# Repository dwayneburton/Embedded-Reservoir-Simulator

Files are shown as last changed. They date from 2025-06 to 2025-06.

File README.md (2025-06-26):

# Embedded Reservoir Simulator
STM32 embedded system project developed in C for the NUCLEO-F401RE microcontroller using STM32CubeIDE. The system simulates a dynamic water reservoir by integrating a servo motor, DC pump motor, ultrasonic distance sensor, RPM sensor, and 7-segment display, all wired on a breadboard. Real-time system data such as water level and motor speed is transmitted via UART and monitored using PuTTY. A corresponding schematic and PCB layout were designed to support hardware integration and future PCB fabrication. 

Reservoir_System
Reservoir_Output
Plant_PCB_Layout
Plant_Schematic
Reservoir_3D-Visual_Top
Reservoir_3D-Visual_Bottom

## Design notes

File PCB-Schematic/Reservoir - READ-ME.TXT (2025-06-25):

LABCENTER PROTEUS TOOL INFORMATION FILE
=======================================

In case of difficulty, please e-mail support@labcenter.co.uk

Tool set up for Proteus layout 'Reservoir.pdsprj'.
CADCAM generated at 2:26:22 PM on November 30, 2024.

File List
---------
Top Copper              : Reservoir - Copper (Top).GBR
Bottom Copper           : Reservoir - Copper (Bottom).GBR
Top Silk Screen         : Reservoir - Silk Screen (Top).GBR
Bottom Silk Screen      : Reservoir - Silk Screen (Bottom).GBR
Top Solder Resist       : Reservoir - Solder Resist (Top).GBR
Bottom Solder Resist    : Reservoir - Solder Resist (Bottom).GBR
Top SMT Paste           : Reservoir - SMT Paste (Top).GBR
Bottom SMT Paste        : Reservoir - SMT Paste (Bottom).GBR
Mechanical 1            : Reservoir - Mechanical.GBR
Top Assembly            : Reservoir - Assembly (Top).GBR
Bottom Assembly         : Reservoir - Assembly (Bottom).GBR
Drill, Plated, 1-16     : Reservoir - Drill Top-Bottom Plated.GBR
Netlist                 : Reservoir - Netlist.IPC

Photoplotter Setup
------------------
Format: X2, ASCII, 4.3, metric, absolute, eob=*, LZO
Bounds: -35mm -32mm 35mm 30mm
Notes:  D=Diameter, S=Side, W=Width, H=Height, C=Chamfer, I=Index

D10	CIRCLE  D=0.381mm                                                         DRAW  Conductor
D11	CIRCLE  D=0.305mm                                                         DRAW  Conductor
D12	CIRCLE  D=0.203mm                                                         DRAW  Conductor
D13	CIRCLE  D=0.152mm                                                         DRAW  Conductor
D14	CIRCLE  D=1.016mm                                                         FLASH ViaPad
D15	CIRCLE  D=0.508mm                                                         FLASH ViaPad
D16	SQUARE  S=1.27mm                                                          FLASH ComponentPad
D17	CIRCLE  D=1.524mm                                                         FLASH ComponentPad
D18	SQUARE  S=2.032mm                                                         FLASH ComponentPad
D19	CIRCLE  D=2.032mm                                                         FLASH ComponentPad
D70	RECT    W=1.27mm              H=3.048mm                                   FLASH SMDPad,CuDef
D71	RECT    W=0.635mm             H=2.032mm                                   FLASH SMDPad,CuDef
D20	RECT    W=2.032mm             H=0.635mm                                   FLASH SMDPad,CuDef
D21	SQUARE  S=0.61mm                                                          FLASH SMDPad,CuDef
D22	CIRCLE  D=0.203mm                                                         DRAW  Profile
D23	RECT    W=0.61mm              H=0.559mm                                   FLASH SMDPad,CuDef
D24	RECT    W=0.559mm             H=0.61mm                                    FLASH SMDPad,CuDef
D25	CIRCLE  D=0.203mm                                                         DRAW  Material
D26	CIRCLE  D=1.27mm                                                          FLASH Material
D27	CIRCLE  D=0.813mm                                                         FLASH Material
D28	PPAD    W=1.524mm             H=1.524mm             I=0                   FLASH Material
D29	CIRCLE  D=1.778mm                                                         FLASH Material
D72	PPAD    W=2.286mm             H=2.286mm             I=1                   FLASH Material
D73	CIRCLE  D=2.286mm                                                         FLASH Material
D30	PPAD    W=2.286mm             H=2.286mm             I=2                   FLASH Material
D31	PPAD    W=1.524mm             H=3.302mm             I=3                   FLASH Material
D32	PPAD    W=0.889mm             H=2.286mm             I=4                   FLASH Material
D33	PPAD    W=2.286mm             H=0.889mm             I=5                   FLASH Material
D34	PPAD    W=0.61mm              H=0.61mm              I=6                   FLASH Material
D35	PPAD    W=0.889mm             H=2.286mm             I=7                   FLASH Material
D36	PPAD    W=0.61mm              H=0.559mm             I=8                   FLASH Material
D37	PPAD    W=0.61mm              H=0.61mm              I=9                   FLASH Material
D38	PPAD    W=0.559mm             H=0.61mm              I=10                  FLASH Material
D39	RECT    W=1.27mm              H=3.048mm                                   FLASH Material
D40	RECT    W=0.635mm             H=2.032mm                                   FLASH Material
D41	RECT    W=2.032mm             H=0.635mm                                   FLASH Material
D42	SQUARE  S=0.61mm                                                          FLASH Material
D43	RECT    W=0.61mm              H=0.559mm                                   FLASH Material
D44	RECT    W=0.559mm             H=0.61mm                                    FLASH Material
D45	CIRCLE  D=0.203mm                                                         DRAW  Slot
D46	CIRCLE  D=0.813mm                                                         DRAW  Material
D47	CIRCLE  D=0.178mm                                                         DRAW  Material
D48	CIRCLE  D=0.33mm                                                          DRAW  Material
D49	CIRCLE  D=0.22mm                                                          DRAW  Material
D50	CIRCLE  D=0.212mm                                                         DRAW  Material
D51	CIRCLE  D=0.051mm                                                         DRAW  Material
D52	CIRCLE  D=1.143mm                                                         DRAW  Material
D53	CIRCLE  D=0.269mm                                                         DRAW  Material
D54	CIRCLE  D=0.572mm                                                         DRAW  Material
D55	CIRCLE  D=0.301mm                                                         DRAW  Material
D56	CIRCLE  D=0.235mm                                                         DRAW  Material
D57	CIRCLE  D=0.05mm                                                          DRAW  Material
D58	CIRCLE  D=0.244mm                                                         DRAW  Material
D59	CIRCLE  D=0.035mm                                                         DRAW  Material
D60	CIRCLE  D=0.085mm                                                         DRAW  Material
D61	CIRCLE  D=0.508mm                                                         DRAW  Material
D62	CIRCLE  D=0.461mm                                                         DRAW  Material
D63	CIRCLE  D=0.473mm                                                         DRAW  Material
D64	CIRCLE  D=0.268mm                                                         DRAW  Material
D65	CIRCLE  D=0.038mm                                                         DRAW  Material
D66	CIRCLE  D=0.381mm                                                         FLASH ViaDrill
D67	CIRCLE  D=0.254mm                                                         FLASH ViaDrill
D68	CIRCLE  D=0.762mm                                                         FLASH ComponentDrill
D69	CIRCLE  D=0.889mm                                                         FLASH ComponentDrill
D74	CIRCLE  D=1.016mm                                                         FLASH ComponentDrill

Layer Stackup
-------------
Top Solder Resist        : 0.01mm     Resist
Top Copper               : 0.035mm    Copper
Core                     : 1.6mm      FR4
Bottom Copper            : 0.035mm    Copper
Bottom Solder Resist     : 0.01mm     Resist

[END OF FILE]

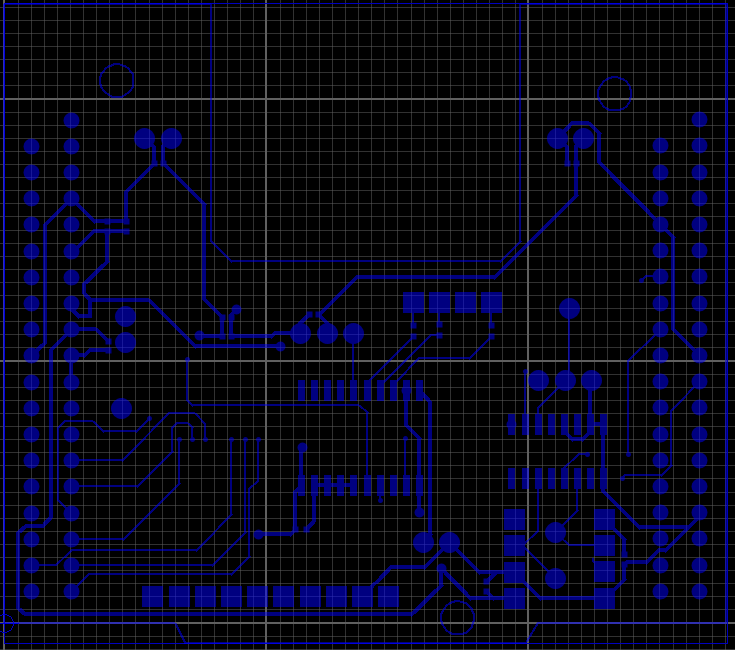
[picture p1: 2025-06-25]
PCB-Schematic/Pictures/Copper (Bottom).PNG

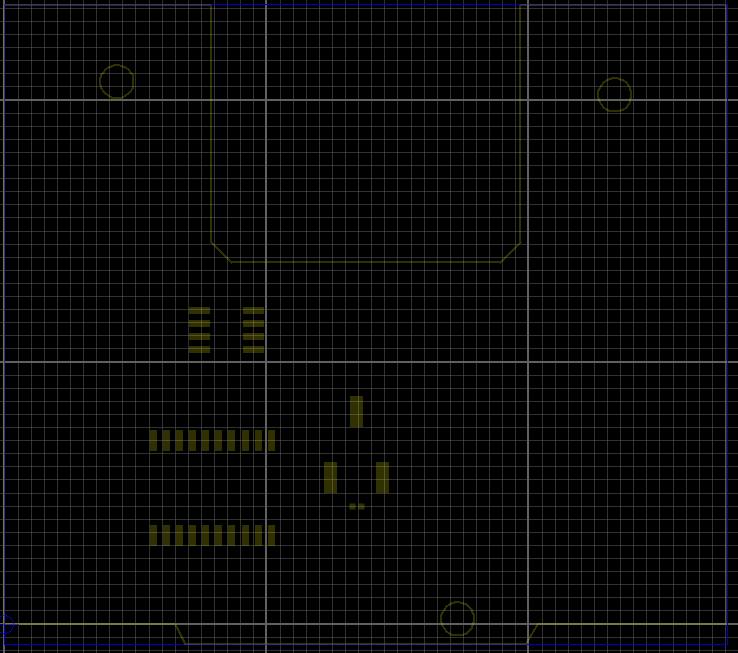
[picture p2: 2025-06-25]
PCB-Schematic/Pictures/SMT Paste (Top).PNG

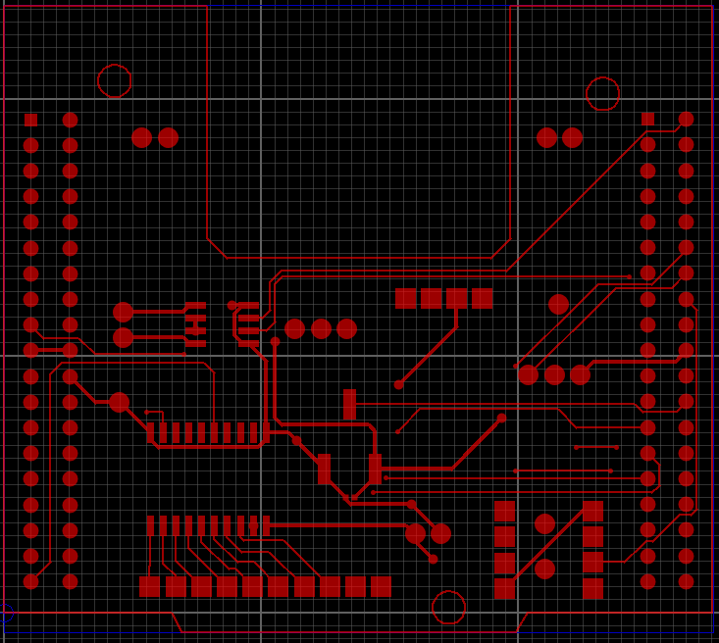
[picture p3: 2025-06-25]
PCB-Schematic/Pictures/Copper (Top).PNG

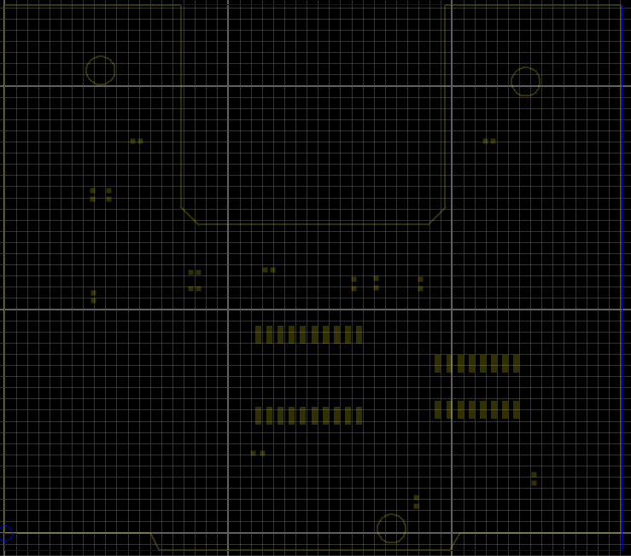
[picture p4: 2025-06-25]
PCB-Schematic/Pictures/SMT Paste (Bottom).PNG

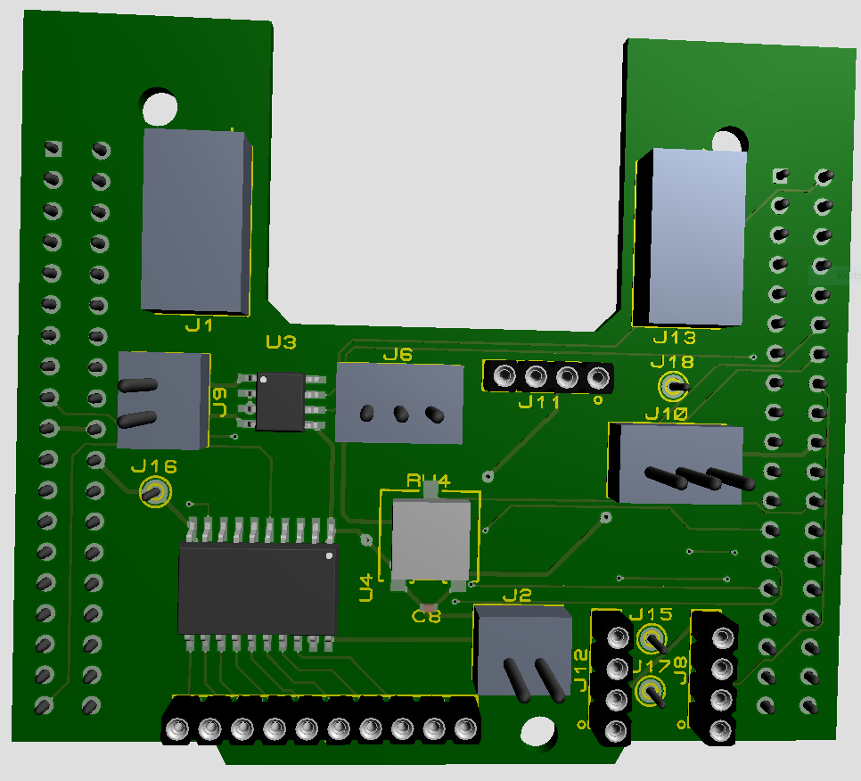
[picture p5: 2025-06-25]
PCB-Schematic/Pictures/3D-Visual (Top).PNG

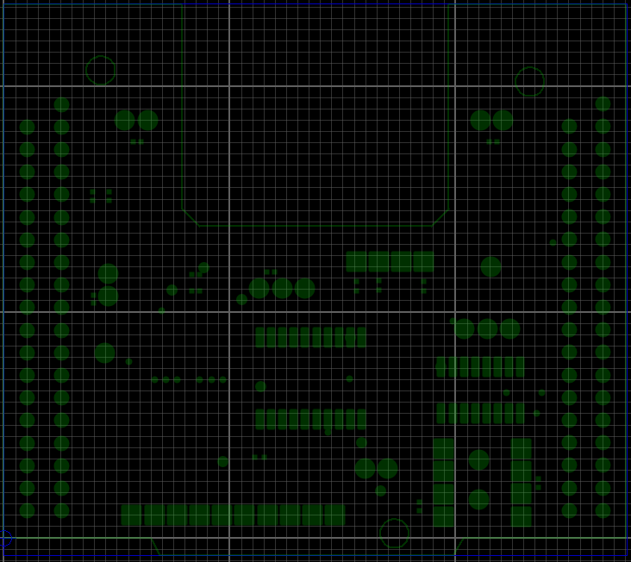
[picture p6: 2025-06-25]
PCB-Schematic/Pictures/Bottom_Resist.PNG

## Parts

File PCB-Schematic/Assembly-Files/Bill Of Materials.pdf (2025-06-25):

## Bill Of Materials for ECE298_RS_ADAPTER

Design Title | ECE298_RS_ADAPTER

### Author Document Number Revision

Design Created | July 7, 2023

### Design Last Modified November 30, 2024 Total Parts In Design 36

11 Capacitors
Quantity | References | Value
2 | C1,C9 | 10000pF
9 | C2-C3,C5-C8,C10-C12 | 100uF
Sub-totals:
4 Resistors
Quantity | References | Value
2 | R1,R3 | 80
1 | R2 | 150
1 | R7 | 1000
Sub-totals:
4 Integrated Circuits
Quantity | References | Value
1 | U2 | ECE298_RS_CMOS4050
1 | U3 | ECE298_RS_L9110
2 | U4-U5 | ECE298_RS_74HCT541
Sub-totals:
17 Miscellaneous
Quantity | References | Value
2 | CN7,CN10 | 1-534236-9
2 | J1,J13 | ECE298_RS_BENCH_POWER
1 | J2 | TIMER BOARD POWER
1 | J6 | MG90S Servo
1 | J8 | HCSR04
1 | J9 | DC MOTOR
1 | J10 | UARTPERIPHERAL
1 | J11 | RGB LED
1 | J12 | RPM SENSOR
1 | J14 | TIMER BOARD
4 | J15-J18 | ECE298_TERMINAL_VIA
1 | RV4 | 10K
Sub-totals:

Totals:

| | November 30, 2024 2:31:16 PM

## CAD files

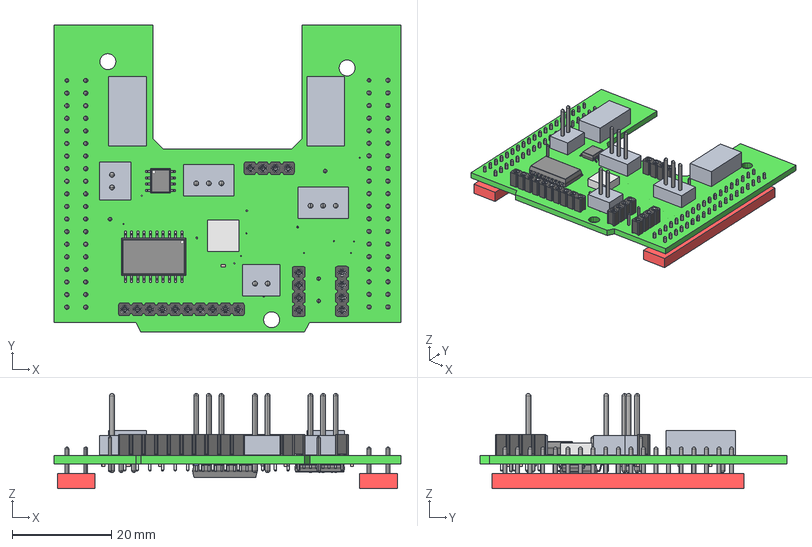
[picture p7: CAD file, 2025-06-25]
PCB-Schematic/Reservoir.STEP
70.0 x 62.0 x 19.2 mm
Layer_1
Pin_1 x 16
Pin_2 x 12
Pin_3 x 4
Pin_4 x 2
Pin_5 x 2
Pin_6 x 2
Pin_7 x 2
Pin_8 x 2
Pin_9 x 2
Pin_10 x 2
Pin_11 x 2
Pin_12 x 2
Pin_13 x 2
Pin_14 x 2
Pin_15 x 2
Pin_16 x 2
Pin_17 x 2
Pin_18 x 2
Pin_19 x 2
Pin_20 x 2
Pin_21 x 2
Pin_22 x 2
Pin_23 x 2
Pin_24 x 2
Pin_25 x 2
Pin_26 x 2
Pin_27 x 2
Pin_28 x 2
Pin_29 x 2
Pin_30 x 2
Pin_31 x 2
Pin_32 x 2
Pin_33 x 2
Pin_34 x 2
Pin_35 x 2
Pin_36 x 2
Pin_37 x 2
Pin_38 x 2

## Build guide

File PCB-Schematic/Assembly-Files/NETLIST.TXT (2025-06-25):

ISIS SCHEMATIC DESCRIPTION FORMAT 8.0
=====================================
Design:   Reservoir
Doc. no.: <NONE>
Revision: <NONE>
Author:   <NONE>
Created:  2023-07-07
Modified: 2024-11-30

*PROPERTIES,0    

*MODELDEFS,0    

*PARTLIST,36   
C1,ECE298_RS_CAP_0U1,10000pF,CODE="Digikey PCC103BQDKR-ND",EID=1E,PACKAGE=CAPC1005X55
C2,ECE298_RS_CAP_0U1,100uF,CODE="Digikey PCC103BQDKR-ND",EID=1F,PACKAGE=CAPC1005X55
C3,ECE298_RS_CAP_0U1,100uF,CODE="Digikey PCC103BQDKR-ND",EID=3,PACKAGE=CAPC1005X55
C5,ECE298_RS_CAP_0U1,100uF,CODE="Digikey PCC103BQDKR-ND",EID=4,PACKAGE=CAPC1005X55
C6,ECE298_RS_CAP_0U1,100uF,CODE="Digikey PCC103BQDKR-ND",EID=5,PACKAGE=CAPC1005X55
C7,ECE298_RS_CAP_0U1,100uF,CODE="Digikey PCC103BQDKR-ND",EID=E,PACKAGE=CAPC1005X55
C8,ECE298_RS_CAP_0U1,100uF,CODE="Digikey PCC103BQDKR-ND",EID=11,PACKAGE=CAPC1005X55
C9,ECE298_RS_CAP_0U1,10000pF,CODE="Digikey PCC103BQDKR-ND",EID=12,PACKAGE=CAPC1005X55
C10,ECE298_RS_CAP_0U1,100uF,CODE="Digikey PCC103BQDKR-ND",EID=13,PACKAGE=CAPC1005X55
C11,ECE298_RS_CAP_0U1,100uF,CODE="Digikey PCC103BQDKR-ND",EID=14,PACKAGE=CAPC1005X55
C12,ECE298_RS_CAP_0U1,100uF,CODE="Digikey PCC103BQDKR-ND",EID=15,PACKAGE=CAPC1005X55
CN7,1-534236-9,1-534236-9,CODE=1-534236-9,EID=25,PACKAGE=ECE298_REVTRANS38DIL-1,SUPPLIER=TE_CONNECTIVITY
CN10,1-534236-9,1-534236-9,CODE=1-534236-9,EID=29,PACKAGE=ECE298_REVTRANS38DIL-1,SUPPLIER=TE_CONNECTIVITY
J1,ECE298_RS_BENCH_POWER,ECE298_RS_BENCH_POWER,EID=1D,PACKAGE=SIL-100-02R
J2,ECE298_RS_2PINHDR,"TIMER BOARD POWER",EID=20,PACKAGE=SIL-100-02
J6,ECE298_RS_3PINHDR,"MG90S Servo",EID=6,PACKAGE=SIL-100-03
J8,ECE298_RS_4PINREC,HCSR04,EID=7,PACKAGE=CONN-SIL4
J9,ECE298_RS_2PINHDR,"DC MOTOR",EID=8,PACKAGE=SIL-100-02
J10,ECE298_RS_3PINHDR,"UART PERIPHERAL",EID=B,PACKAGE=SIL-100-03
J11,ECE298_RS_4PINREC,"RGB LED",EID=C,PACKAGE=CONN-SIL4
J12,ECE298_RS_4PINREC,"RPM SENSOR",EID=D,PACKAGE=CONN-SIL4
J13,ECE298_RS_BENCH_POWER,ECE298_RS_BENCH_POWER,EID=F,PACKAGE=SIL-100-02R
J14,ECE298_RS_10PINREC,"TIMER BOARD",EID=10,PACKAGE=CONN-SIL10
J15,ECE298_TERMINAL_VIA,ECE298_TERMINAL_VIA,EID=17,PACKAGE=PIN
J16,ECE298_TERMINAL_VIA,ECE298_TERMINAL_VIA,EID=18,PACKAGE=PIN
J17,ECE298_TERMINAL_VIA,ECE298_TERMINAL_VIA,EID=19,PACKAGE=PIN
J18,ECE298_TERMINAL_VIA,ECE298_TERMINAL_VIA,EID=1A,PACKAGE=PIN
R1,9C04021A1500JLHF3,80,CODE="Digikey 311-150JDKR-ND",EID=1,PACKAGE=RESC1005X40,PRIMTYPE=RESISTOR
R2,9C04021A1800JLHF3,150,CODE="Digikey 311-180JCT-ND",EID=2,PACKAGE=RESC1005X40,PRIMTYPE=RESISTOR
R3,9C04021A1500JLHF3,80,CODE="Digikey 311-150JDKR-ND",EID=24,PACKAGE=RESC1005X40,PRIMTYPE=RESISTOR
R7,9C04021A1500JLHF3,1000,CODE="Digikey 311-150JDKR-ND",EID=1B,PACKAGE=RESC1005X40,PRIMTYPE=RESISTOR
RV4,ECE298_RS_POT10K,10K,CODE="Digikey 3361P-103GLFDKR-ND",EID=9,PACKAGE=TRIM_3361P,STATE=5
U2,ECE298_RS_CMOS4050,ECE298_RS_CMOS4050,EID_A=21,EID_B=22,EID_C=23,EID_D=26,EID_E=27,EID_F=28,ITFMOD=CMOS,MODFILE=40BUF,PACKAGE=SO16,VDD=+3.3V,VSS=GND
U3,ECE298_RS_L9110,ECE298_RS_L9110,EID=A,ITFMOD=TTL,PACKAGE=SO8
U4,ECE298_RS_74HCT541,ECE298_RS_74HCT541,EID=16,GND=GND,PACKAGE=SO20W,PINSWAP="1,19",VCC=+5.0V
U5,ECE298_RS_74HCT541,ECE298_RS_74HCT541,EID=1C,GND=GND,PACKAGE=SO20W,PINSWAP="1,19",VCC=+5.0V

*NETLIST,47   
GRN,3,CLASS=SIGNAL
GRN,LBL
R1,PS,1
J11,PS,4

GRN_5V,3,CLASS=SIGNAL
GRN_5V,LBL
R1,PS,2
U5,TS,16

RED,3,CLASS=SIGNAL
RED,LBL
R2,PS,1
J11,PS,3

RED_5V,3,CLASS=SIGNAL
RED_5V,LBL
R2,PS,2
U5,TS,17

PWM,3,CLASS=SIGNAL
PWM,LBL
J6,PS,3
U5,TS,15

ECHO,4,CLASS=SIGNAL
ECHO,LBL
J8,PS,3
J15,PS,1
U2,IP,11

OA,3,CLASS=POWER
OA,LBL
J9,PS,1
U3,OP,1

OB,3,CLASS=POWER
OB,LBL
J9,PS,2
U3,OP,4

RXD,4,CLASS=SIGNAL
RXD,LBL
J10,PS,2
U2,IP,3
J18,PS,1

BLU,3,CLASS=SIGNAL
BLU,LBL
J11,PS,1
R3,PS,1

D0,4,CLASS=SIGNAL
D0,LBL
J12,PS,3
J17,PS,1
U2,IP,14

DIGIT_A3,3,CLASS=SIGNAL
DIGIT_A3,LBL
U4,TS,18
J14,PS,3

DIGIT_A2,3,CLASS=SIGNAL
DIGIT_A2,LBL
U4,TS,17
J14,PS,4

DIGIT_A1,3,CLASS=SIGNAL
DIGIT_A1,LBL
U4,TS,16
J14,PS,5

DIGIT_A0,3,CLASS=SIGNAL
DIGIT_A0,LBL
U4,TS,15
J14,PS,6

DIGIT_B3,3,CLASS=SIGNAL
DIGIT_B3,LBL
U4,TS,14
J14,PS,7

DIGIT_B2,3,CLASS=SIGNAL
DIGIT_B2,LBL
U4,TS,13
J14,PS,8

DIGIT_B1,3,CLASS=SIGNAL
DIGIT_B1,LBL
U4,TS,12
J14,PS,9

DIGIT_B0,3,CLASS=SIGNAL
DIGIT_B0,LBL
U4,TS,11
J14,PS,10

DRAIN,6,CLASS=POWER
DRAIN,LBL
R7,PS,1
U5,IP,6
U5,IP,7
U5,IP,8
U5,IP,9

BLU_5V,3,CLASS=SIGNAL
BLU_5V,LBL
U5,TS,18
R3,PS,2

PA0,3,CLASS=SIGNAL
PA0,GT
CN7,PS,28
U4,IP,6

PA1,3,CLASS=SIGNAL
PA1,GT
CN7,PS,30
U4,IP,7

PA4,3,CLASS=SIGNAL
PA4,GT
CN7,PS,32
U4,IP,9

PB0,3,CLASS=SIGNAL
PB0,GT
CN7,PS,34
U4,IP,8

PC2,3,CLASS=SIGNAL
PC2,GT
CN7,PS,35
U4,IP,4

PC1,3,CLASS=SIGNAL
PC1,GT
CN7,PS,36
U4,IP,3

PC3,3,CLASS=SIGNAL
PC3,GT
CN7,PS,37
U4,IP,5

PC0,3,CLASS=SIGNAL
PC0,GT
CN7,PS,38
U4,IP,2

PA12,3,CLASS=SIGNAL
PA12,GT
CN10,PS,12
U2,OP,2

PA6,4,CLASS=SIGNAL
PA6,GT
PWM CH1,LBL
CN10,PS,13
U3,IP,6

PA11,4,CLASS=SIGNAL
PA11,GT
TXD,LBL
CN10,PS,14
J10,PS,1

PB12,4,CLASS=SIGNAL
PB12,GT
TRIG,LBL
CN10,PS,16
J8,PS,2

PC8,4,CLASS=SIGNAL
PC8,GT
PWM CH2,LBL
CN10,PS,2
U3,IP,7

PB1,3,CLASS=SIGNAL
PB1,GT
CN10,PS,24
RV4,PS,3

PB10,3,CLASS=SIGNAL
PB10,GT
CN10,PS,25
U5,IP,2

PB4,3,CLASS=SIGNAL
PB4,GT
CN10,PS,27
U5,IP,4

PB5,3,CLASS=SIGNAL
PB5,GT
CN10,PS,29
U5,IP,3

PA15,3,CLASS=SIGNAL
PA15,GT
CN7,PS,17
U5,IP,5

PB2,3,CLASS=SIGNAL
PB2,GT
U2,OP,15
CN10,PS,22

PB6,3,CLASS=SIGNAL
PB6,GT
U2,OP,12
CN10,PS,17

{NC},58
A0,LBL
J14,PS,1
U2,PS,13
U2,PS,16
U2,OP,6
U2,OP,4
CN10,PS,31
U2,OP,10
CN10,PS,15
CN10,PS,37
CN10,PS,35
CN10,PS,34
CN10,PS,30
CN10,PS,28
CN10,PS,33
CN10,PS,26
CN10,PS,23
CN10,PS,21
CN10,PS,19
CN10,PS,18
CN10,PS,11
CN10,PS,6
CN10,PS,5
CN10,PS,4
CN10,PS,3
CN10,PS,1
CN7,PS,1
CN7,PS,2
CN7,PS,3
CN7,PS,13
CN7,PS,15
CN7,PS,21
CN7,PS,23
CN7,PS,14
CN10,PS,8
CN10,PS,7
CN10,PS,38
CN10,PS,36
CN10,PS,10
CN7,PS,9
CN7,PS,7
CN7,PS,6
CN7,PS,5
CN7,PS,4
CN7,PS,33
CN7,PS,31
CN7,PS,29
CN7,PS,27
CN7,PS,26
CN7,PS,25
CN7,PS,24
CN7,PS,11
CN7,PS,10
U5,TS,14
U5,TS,13
U5,TS,12
U5,TS,11
J12,PS,4

+3.3V,8,CLASS=POWER
+3.3V,PR
U2,PP,1
CN7,PS,16
CN7,PS,12
C8,PS,1
RV4,PS,2
C5,PS,1
C2,PS,1

+5.0V,11,CLASS=POWER
+5.0V,PR
VCC,LBL
CN7,PS,18
J2,PS,1
U5,PP,20
U4,PP,20
J12,PS,1
C11,PS,1
J8,PS,4
C10,PS,1
C6,PS,1

+5V_EXT,5,CLASS=POWER
+5V_EXT,PR
J13,PS,1
C7,PS,1
J6,PS,2
C12,PS,1

+6V_EXT,7,CLASS=POWER
+6V_EXT,PR
U3,PP,2
U3,PP,3
C9,PS,1
C1,PS,1
J1,PS,1
C3,PS,1

GND,43,CLASS=POWER
GND,PR
J14,PS,2
U2,PP,8
U2,IP,7
U2,IP,5
U2,IP,9
CN10,PS,9
CN10,PS,32
CN10,PS,20
CN7,PS,8
CN7,PS,22
CN7,PS,20
CN7,PS,19
J2,PS,2
U5,PP,10
J16,PS,1
U4,PP,10
C12,PS,2
U5,IP,19
U5,IP,1
R7,PS,2
C11,PS,2
C10,PS,2
C9,PS,2
C1,PS,2
U4,IP,1
U4,IP,19
J13,PS,2
C7,PS,2
J12,PS,2
J11,PS,2
J10,PS,3
J8,PS,1
U3,PP,5
U3,PP,8
C8,PS,2
RV4,PS,1
J6,PS,1
C6,PS,2
C5,PS,2
C2,PS,2
C3,PS,2
J1,PS,2

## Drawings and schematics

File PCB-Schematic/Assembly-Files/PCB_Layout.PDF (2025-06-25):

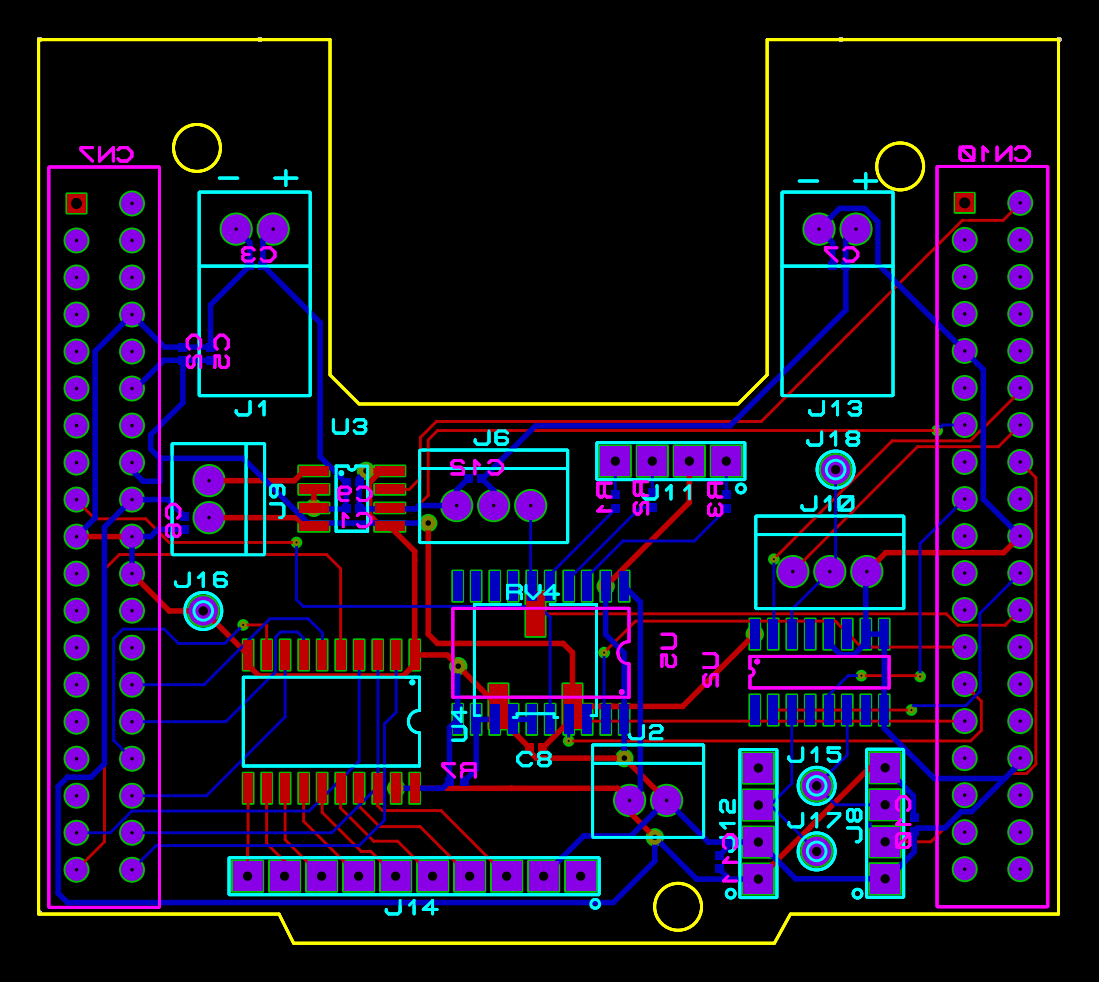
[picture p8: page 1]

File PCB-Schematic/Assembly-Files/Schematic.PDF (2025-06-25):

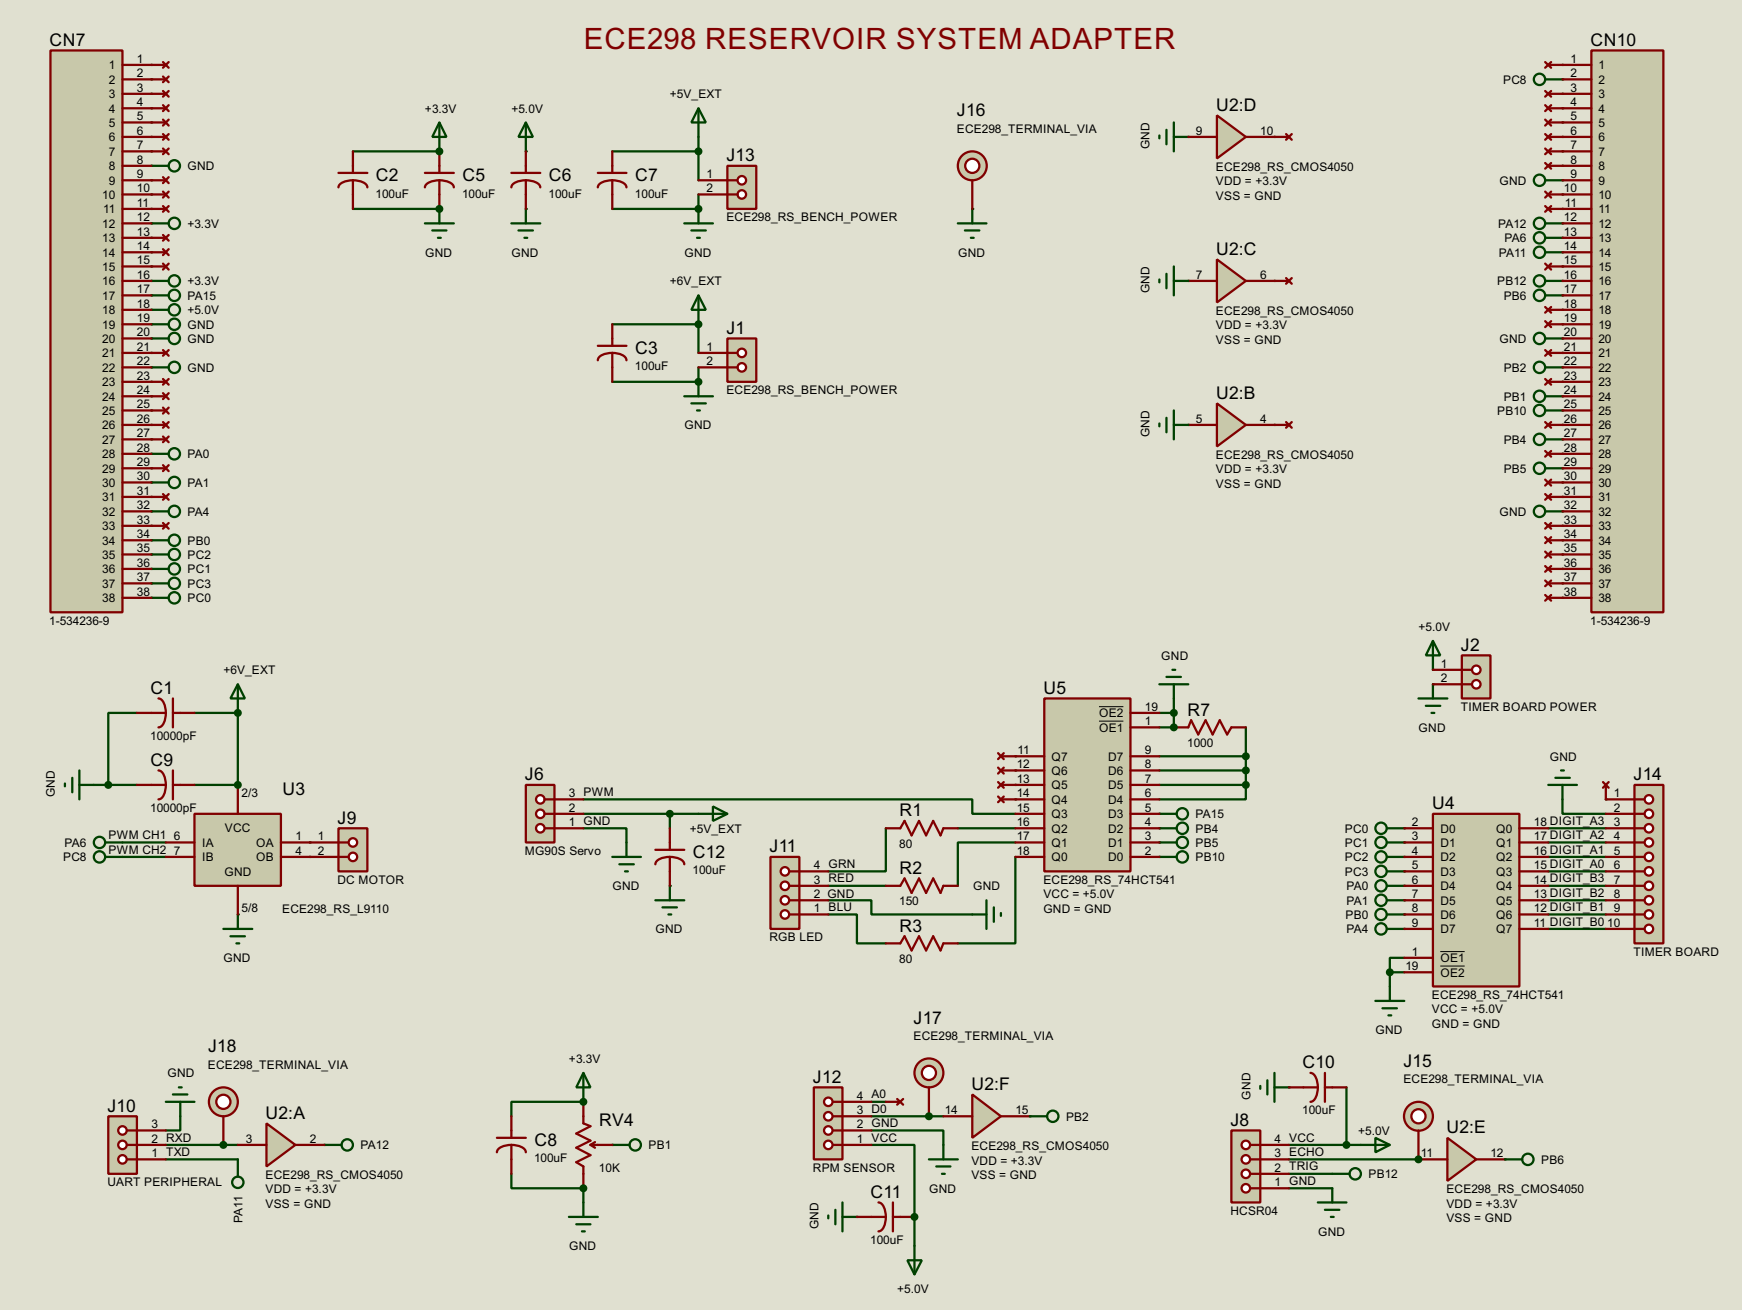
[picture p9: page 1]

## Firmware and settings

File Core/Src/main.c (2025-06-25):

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
/* Includes ------------------------------------------------------------------*/
#include "main.h"

/* USER CODE BEGIN Includes */
#include <string.h>
#include <stdio.h>
#include <time.h>
#include <stdlib.h>
/* USER CODE END Includes */

ADC_HandleTypeDef hadc1;

TIM_HandleTypeDef htim2;
TIM_HandleTypeDef htim3;
TIM_HandleTypeDef htim4;
TIM_HandleTypeDef htim5;

UART_HandleTypeDef huart2;
UART_HandleTypeDef huart6;

/* USER CODE BEGIN PV */
volatile uint8_t clock_hours = 0;
volatile uint8_t clock_mins = 0;
volatile uint8_t clock_secs = 0;
volatile uint8_t wall_clock_hr_update_flag = 0;

volatile uint8_t hcsr04_Rx_flag = 0; // Reset the interrupt flag for the HCSR04
volatile uint8_t first_edge = 0; // Set it back to false
volatile uint16_t time_edge1 = 0;
volatile uint16_t time_edge2 = 0;

volatile uint16_t rpm_tick_count = 0;

uint8_t empty = 0;
uint8_t byte[2];
uint8_t rcv_intpt_flag = 0;
uint8_t txd_msg_buffer[64] = {0};

uint16_t time_diff = 0;
int filled = 0;
int distance = 0;

uint8_t counter_tens = 0;
uint8_t counter_ones = 0;
uint8_t bottom_distance = 65; //distance to bottom in cm
uint8_t top_distance = 10; //distance to top in cm
uint8_t rpm = 0;

int TIM2_CH1_DCVAL = 500;

/* USER CODE END PV */

void SystemClock_Config(void);
static void MX_GPIO_Init(void);
static void MX_USART2_UART_Init(void);
static void MX_USART6_UART_Init(void);
static void MX_ADC1_Init(void);
static void MX_TIM3_Init(void);
static void MX_TIM2_Init(void);
static void MX_TIM4_Init(void);
static void MX_TIM5_Init(void);
/* USER CODE BEGIN PFP */
static void ADC_Select_CH(int CH);
/* USER CODE END PFP */

/* USER CODE BEGIN 0 */


void ADC_Select_CH(int CH)
{
    ADC_ChannelConfTypeDef sConfig = {0};
    switch(CH)
    {
        case 0:
            sConfig.Channel = ADC_CHANNEL_0;
            sConfig.Rank = 1;
            if (HAL_ADC_ConfigChannel(&hadc1, &sConfig) != HAL_OK)
            {
                Error_Handler();
            }
            break;
        case 1:
            sConfig.Channel = ADC_CHANNEL_1;
            sConfig.Rank = 1;
            if (HAL_ADC_ConfigChannel(&hadc1, &sConfig) != HAL_OK)
            {
                Error_Handler();
            }
            break;
        case 2:
            sConfig.Channel = ADC_CHANNEL_2;
            sConfig.Rank = 1;
            if (HAL_ADC_ConfigChannel(&hadc1, &sConfig) != HAL_OK)
            {
                Error_Handler();
            }
            break;
        case 3:
            sConfig.Channel = ADC_CHANNEL_3;
            sConfig.Rank = 1;
            if (HAL_ADC_ConfigChannel(&hadc1, &sConfig) != HAL_OK)
            {
                Error_Handler();
            }
            break;
        case 4:
            sConfig.Channel = ADC_CHANNEL_4;
            sConfig.Rank = 1;
            if (HAL_ADC_ConfigChannel(&hadc1, &sConfig) != HAL_OK)
            {
                Error_Handler();
            }
            break;
        case 5:
            sConfig.Channel = ADC_CHANNEL_5;
            sConfig.Rank = 1;
            if (HAL_ADC_ConfigChannel(&hadc1, &sConfig) != HAL_OK)
            {
                Error_Handler();
            }
            break;
        case 6:
            sConfig.Channel = ADC_CHANNEL_6;
            sConfig.Rank = 1;
            if (HAL_ADC_ConfigChannel(&hadc1, &sConfig) != HAL_OK)
            {
                Error_Handler();
            }
            break;
        case 7:
            sConfig.Channel = ADC_CHANNEL_7;
            sConfig.Rank = 1;
            if (HAL_ADC_ConfigChannel(&hadc1, &sConfig) != HAL_OK)
            {
                Error_Handler();
            }
            break;
        case 8:
            sConfig.Channel = ADC_CHANNEL_8;
            sConfig.Rank = 1;
            if (HAL_ADC_ConfigChannel(&hadc1, &sConfig) != HAL_OK)
            {
                Error_Handler();
            }
            break;
        case 9:
            sConfig.Channel = ADC_CHANNEL_9;
            sConfig.Rank = 1;
            if (HAL_ADC_ConfigChannel(&hadc1, &sConfig) != HAL_OK)
            {
                Error_Handler();
            }
            break;
        case 10:
            sConfig.Channel = ADC_CHANNEL_10;
            sConfig.Rank = 1;
            if (HAL_ADC_ConfigChannel(&hadc1, &sConfig) != HAL_OK)
            {
                Error_Handler();
            }
            break;
        case 11:
            sConfig.Channel = ADC_CHANNEL_11;
            sConfig.Rank = 1;
            if (HAL_ADC_ConfigChannel(&hadc1, &sConfig) != HAL_OK)
            {
                Error_Handler();
            }
            break;
        case 12:
            sConfig.Channel = ADC_CHANNEL_12;
            sConfig.Rank = 1;
            if (HAL_ADC_ConfigChannel(&hadc1, &sConfig) != HAL_OK)
            {
                Error_Handler();
            }
            break;
        case 13:
            sConfig.Channel = ADC_CHANNEL_13;
            sConfig.Rank = 1;
            if (HAL_ADC_ConfigChannel(&hadc1, &sConfig) != HAL_OK)
            {
                Error_Handler();
            }
            break;
        case 14:
            sConfig.Channel = ADC_CHANNEL_14;
            sConfig.Rank = 1;
            if (HAL_ADC_ConfigChannel(&hadc1, &sConfig) != HAL_OK)
            {
                Error_Handler();
            }
            break;
        case 15:
            sConfig.Channel = ADC_CHANNEL_15;
            sConfig.Rank = 1;
            if (HAL_ADC_ConfigChannel(&hadc1, &sConfig) != HAL_OK)
            {
                Error_Handler();
            }
            break;
    }
}


void DIGITS_Display(uint8_t DIGIT)
{
	uint8_t DIGIT_B = DIGIT % 10;
	uint8_t DIGIT_A = (DIGIT - DIGIT_B) / 10;

	uint8_t DIGITA_VAL = 0x0F & DIGIT_A; //mask off higher4 bits
	 int Abit0 = (DIGITA_VAL ) & 1;  	// extract Abit0 of the 4-bit value
	 int Abit1 = (DIGITA_VAL >> 1) & 1;  // extract Abit1 of the 4-bit value
	 int Abit2 = (DIGITA_VAL >> 2) & 1;  // extract Abit2 of the 4-bit value
	 int Abit3 = (DIGITA_VAL >> 3) & 1;  // extract Abit3 of the 4-bit value

	 uint8_t DIGITB_VAL = 0x0F & DIGIT_B; //mask off higher4 bits
	 int Bbit0 = (DIGITB_VAL ) & 1;  	// extract Bbit0 of the 4-bit value
	 int Bbit1 = (DIGITB_VAL >> 1) & 1;  // extract Bbit1 of the 4-bit value
	 int Bbit2 = (DIGITB_VAL >> 2) & 1;  // extract Bbit2 of the 4-bit value
	 int Bbit3 = (DIGITB_VAL >> 3) & 1;  // extract Bbit3 of the 4-bit value

	 if (Abit0 == (0))
	 {
		 HAL_GPIO_WritePin(GPIOC, DIGIT_A0_Pin, GPIO_PIN_RESET);
	 }
	 else
	 {
		 HAL_GPIO_WritePin(GPIOC, DIGIT_A0_Pin, GPIO_PIN_SET);

	 }
	 if (Abit1 == (0))
	 {
		 HAL_GPIO_WritePin(GPIOC, DIGIT_A1_Pin, GPIO_PIN_RESET);
	 }
	 else
	 {
		 HAL_GPIO_WritePin(GPIOC, DIGIT_A1_Pin, GPIO_PIN_SET);

	 }
	 if (Abit2 == (0))
	 {
		 HAL_GPIO_WritePin(GPIOC, DIGIT_A2_Pin, GPIO_PIN_RESET);
	 }
	 else
	 {
		 HAL_GPIO_WritePin(GPIOC, DIGIT_A2_Pin, GPIO_PIN_SET);

	 }
	 if (Abit3 == (0))
	 {
		 HAL_GPIO_WritePin(GPIOC, DIGIT_A3_Pin, GPIO_PIN_RESET);
	 }
	 else
	 {
		 HAL_GPIO_WritePin(GPIOC, DIGIT_A3_Pin, GPIO_PIN_SET);

	 }


	 if (Bbit0 == (0))
	 {
		 HAL_GPIO_WritePin(GPIOA, DIGIT_B0_Pin, GPIO_PIN_RESET);
	 }
	 else
	 {
		 HAL_GPIO_WritePin(GPIOA, DIGIT_B0_Pin, GPIO_PIN_SET);

	 }
	 if (Bbit1 == (0))
	 {
		 HAL_GPIO_WritePin(GPIOB, DIGIT_B1_Pin, GPIO_PIN_RESET);
	 }
	 else
	 {
		 HAL_GPIO_WritePin(GPIOB, DIGIT_B1_Pin, GPIO_PIN_SET);

	 }
	 if (Bbit2 == (0))
	 {
		 HAL_GPIO_WritePin(GPIOA, DIGIT_B2_Pin, GPIO_PIN_RESET);
	 }
	 else
	 {
		 HAL_GPIO_WritePin(GPIOA, DIGIT_B2_Pin, GPIO_PIN_SET);

	 }
	 if (Bbit3 == (0))
	 {
		 HAL_GPIO_WritePin(GPIOA, DIGIT_B3_Pin, GPIO_PIN_RESET);
	 }
	 else
	 {
		 HAL_GPIO_WritePin(GPIOA, DIGIT_B3_Pin, GPIO_PIN_SET);

	 }
}

void HCSR04_TRIG_PULSE(void)
{
	HAL_GPIO_WritePin(HCSR04_TRIG_GPIO_Port, HCSR04_TRIG_Pin, GPIO_PIN_SET);
	for (int j = 0; j != 48; j = j + 1) {}
	HAL_GPIO_WritePin(HCSR04_TRIG_GPIO_Port, HCSR04_TRIG_Pin, GPIO_PIN_RESET);
	HAL_Delay(30);
}

void MOTOR_Run(int speed)
{
	if(speed >= 0) {
		TIM3->CCR3 = ((float)speed/100)*60000;
		TIM3->CCR1 = 0;
	} else {
		TIM3->CCR1 = ((float)speed/-100)*60000;
		TIM3->CCR3 = 0;
	}
}

void SERVO_Run(int position)
{
	int TIM2_CH1_STEP = 20;
	while(TIM2_CH1_DCVAL != position) {
		if(TIM2_CH1_DCVAL < position){
			TIM2_CH1_DCVAL += TIM2_CH1_STEP;
		}else if (TIM2_CH1_DCVAL > position){
			TIM2_CH1_DCVAL -= TIM2_CH1_STEP;
		}
		TIM2->CCR1 = TIM2_CH1_DCVAL;
		HAL_Delay(5);
	}
}

void RGBLED_Run(uint8_t colour)
{
	switch(colour)
	{
	case 0: // purple
		HAL_GPIO_WritePin(GPIOB, BLU_Pin, GPIO_PIN_SET);
		HAL_GPIO_WritePin(GPIOB, GRN_Pin, GPIO_PIN_RESET);
		HAL_GPIO_WritePin(GPIOB, RED_Pin, GPIO_PIN_SET);
		break;
	case 1: // red
		HAL_GPIO_WritePin(GPIOB, BLU_Pin, GPIO_PIN_RESET);
		HAL_GPIO_WritePin(GPIOB, GRN_Pin, GPIO_PIN_RESET);
		HAL_GPIO_WritePin(GPIOB, RED_Pin, GPIO_PIN_SET);
		break;
	case 2: // green
		HAL_GPIO_WritePin(GPIOB, BLU_Pin, GPIO_PIN_RESET);
		HAL_GPIO_WritePin(GPIOB, GRN_Pin, GPIO_PIN_SET);
		HAL_GPIO_WritePin(GPIOB, RED_Pin, GPIO_PIN_RESET);
		break;
	case 3: // blue
		HAL_GPIO_WritePin(GPIOB, BLU_Pin, GPIO_PIN_SET);
		HAL_GPIO_WritePin(GPIOB, GRN_Pin, GPIO_PIN_RESET);
		HAL_GPIO_WritePin(GPIOB, RED_Pin, GPIO_PIN_RESET);
		break;
	case 4: // none
		HAL_GPIO_WritePin(GPIOB, BLU_Pin, GPIO_PIN_RESET);
		HAL_GPIO_WritePin(GPIOB, GRN_Pin, GPIO_PIN_RESET);
		HAL_GPIO_WritePin(GPIOB, RED_Pin, GPIO_PIN_RESET);
		break;
	case 5: // white
		HAL_GPIO_WritePin(GPIOB, BLU_Pin, GPIO_PIN_SET);
		HAL_GPIO_WritePin(GPIOB, GRN_Pin, GPIO_PIN_SET);
		HAL_GPIO_WritePin(GPIOB, RED_Pin, GPIO_PIN_SET);
		break;
	}
}

int generate_random(int min, int max){
	return (rand() % (max-min+1))+ min;
}
/* USER CODE END 0 */

/**
  * @brief  The application entry point.
  * @retval int
  */
int main(void)
{

  /* MCU Configuration--------------------------------------------------------*/

  /* Reset of all peripherals, Initializes the Flash interface and the Systick. */
  HAL_Init();

  /* Configure the system clock */
  SystemClock_Config();

  /* Initialize all configured peripherals */
  MX_GPIO_Init();
  MX_USART2_UART_Init();
  MX_USART6_UART_Init();
  MX_ADC1_Init();
  MX_TIM3_Init();
  MX_TIM2_Init();
  MX_TIM4_Init();
  MX_TIM5_Init();
  /* USER CODE BEGIN 2 */

  HAL_TIM_Base_Start(&htim2);
  HAL_TIM_PWM_Start(&htim2, TIM_CHANNEL_1);
  TIM3->PSC = 16-1;
  TIM3->ARR = 20000-1;
  TIM3->CCR1 = TIM2_CH1_DCVAL;

  //HAL_TIM_Base_Init(&htim3);
  HAL_TIM_PWM_Start(&htim3, TIM_CHANNEL_1);
  HAL_TIM_PWM_Start(&htim3, TIM_CHANNEL_3);
  TIM3->PSC = 0;
  TIM3->ARR = 60000;
  TIM3->CCR1 = 0;
  TIM3->CCR3 = 0;

  HAL_TIM_Base_Init(&htim4);
  HAL_TIM_Base_Start(&htim4);
  HAL_TIM_IC_Start_IT(&htim4, TIM_CHANNEL_1);

  HAL_TIM_Base_Start_IT(&htim5);
  clock_hours = 0;
  clock_mins = 0;
  clock_secs = 0;
  /* USER CODE END 2 */
  /* Infinite loop */
  /* USER CODE BEGIN WHILE */

  uint8_t pipe_connection[4] = {0};
  uint8_t pipe_pwm_mode[4] = {0};
  uint8_t current_time = 0;
  uint8_t start_time[4] = {0};
  uint8_t end_time[4] = {0};

  sprintf((char*)txd_msg_buffer, "\r\n\nSETUP MODE");
  HAL_UART_Transmit(&huart6, txd_msg_buffer, strlen((char*)txd_msg_buffer), 1000);
  HAL_Delay(500);

  sprintf((char*)txd_msg_buffer,"\r\n\nFIRST PIPELINE CHOICE FOR CONNECTION: ");
  HAL_UART_Transmit(&huart6, txd_msg_buffer, strlen((char*)txd_msg_buffer),1000);
  rcv_intpt_flag = 00;
  HAL_UART_Receive_IT(&huart6, &byte, 1);
  while(rcv_intpt_flag == (00)) {}
  pipe_connection[0] = (byte[0]-'0');
  sprintf((char*)txd_msg_buffer,"\r\nFIRST PIPELINE CHOICE FOR MOTOR PWM: ");
  HAL_UART_Transmit(&huart6, txd_msg_buffer, strlen((char*)txd_msg_buffer),1000);
  rcv_intpt_flag = 00;
  HAL_UART_Receive_IT(&huart6, &byte, 2);
  while(rcv_intpt_flag == (00)) {}
  pipe_pwm_mode[0] = (byte[0]-'0');

  sprintf((char*)txd_msg_buffer,"\r\nSECOND ZONE CHOICE FOR CONNECTION: ");
  HAL_UART_Transmit(&huart6, txd_msg_buffer, strlen((char*)txd_msg_buffer),1000);
  rcv_intpt_flag = 00;
  HAL_UART_Receive_IT(&huart6, &byte, 1);
  while(rcv_intpt_flag == (00)) {}
  pipe_connection[1] = (byte[0]-'0');
  sprintf((char*)txd_msg_buffer,"\r\nSECOND ZONE CHOICE FOR MOTOR PWM: ");
  HAL_UART_Transmit(&huart6, txd_msg_buffer, strlen((char*)txd_msg_buffer),1000);
  rcv_intpt_flag = 00;
  HAL_UART_Receive_IT(&huart6, &byte, 1);
  while(rcv_intpt_flag == (00)) {}
  pipe_pwm_mode[1] = (byte[0]-'0');

  sprintf((char*)txd_msg_buffer,"\r\nTHIRD ZONE CHOICE FOR CONNECTION: ");
  HAL_UART_Transmit(&huart6, txd_msg_buffer, strlen((char*)txd_msg_buffer),1000);
  rcv_intpt_flag = 00;
  HAL_UART_Receive_IT(&huart6, &byte, 1);
  while(rcv_intpt_flag == (00)) {}
  pipe_connection[2] = (byte[0]-'0');
  sprintf((char*)txd_msg_buffer,"\r\nTHIRD ZONE CHOICE FOR MOTOR PWM: ");
  HAL_UART_Transmit(&huart6, txd_msg_buffer, strlen((char*)txd_msg_buffer),1000);
  rcv_intpt_flag = 00;
  HAL_UART_Receive_IT(&huart6, &byte, 1);
  while(rcv_intpt_flag == (00)) {}
  pipe_pwm_mode[2] = (byte[0]-'0');

  sprintf((char*)txd_msg_buffer,"\r\nFOURTH ZONE CHOICE FOR CONNECTION: ");
  HAL_UART_Transmit(&huart6, txd_msg_buffer, strlen((char*)txd_msg_buffer),1000);
  rcv_intpt_flag = 00;
  HAL_UART_Receive_IT(&huart6, &byte, 1);
  while(rcv_intpt_flag == (00)) {}
  pipe_connection[3] = (byte[0]-'0');
  sprintf((char*)txd_msg_buffer,"\r\nFOURTH ZONE CHOICE FOR MOTOR PWM: ");
  HAL_UART_Transmit(&huart6, txd_msg_buffer, strlen((char*)txd_msg_buffer),1000);
  rcv_intpt_flag = 00;
  HAL_UART_Receive_IT(&huart6, &byte, 1);
  while(rcv_intpt_flag == (00)) {}
  pipe_pwm_mode[3] = (byte[0]-'0');


  sprintf((char*)txd_msg_buffer,"\r\n\nCURRENT WALL CLOCK TIME: ");
  HAL_UART_Transmit(&huart6, txd_msg_buffer, strlen((char*)txd_msg_buffer),1000);
  rcv_intpt_flag = 00;
  HAL_UART_Receive_IT(&huart6, &byte, 2);
  while(rcv_intpt_flag == (00)) {}
  current_time = (byte[0] - '0') * 10 + (byte[1] - '0');

  sprintf((char*)txd_msg_buffer,"\r\nINLET WALL CLOCK START TIME: ");
  HAL_UART_Transmit(&huart6, txd_msg_buffer, strlen((char*)txd_msg_buffer),1000);
  rcv_intpt_flag = 00;
  HAL_UART_Receive_IT(&huart6, &byte, 2);
  while(rcv_intpt_flag == (00)) {}
  start_time[0] = (byte[0] - '0') * 10 + (byte[1] - '0');
  sprintf((char*)txd_msg_buffer,"\r\nINLET WALL CLOCK STOP TIME: ");
  HAL_UART_Transmit(&huart6, txd_msg_buffer, strlen((char*)txd_msg_buffer),1000);
  rcv_intpt_flag = 00;
  HAL_UART_Receive_IT(&huart6, &byte, 2);
  while(rcv_intpt_flag == (00)) {}
  end_time[0] = (byte[0] - '0') * 10 + (byte[1] - '0');

  sprintf((char*)txd_msg_buffer,"\r\nFIRST ZONE CHOICE WALL CLOCK START TIME: ");
  HAL_UART_Transmit(&huart6, txd_msg_buffer, strlen((char*)txd_msg_buffer),1000);
  rcv_intpt_flag = 00;
  HAL_UART_Receive_IT(&huart6, &byte, 2);
  while(rcv_intpt_flag == (00)) {}
  start_time[1] = (byte[0] - '0') * 10 + (byte[1] - '0');
  sprintf((char*)txd_msg_buffer,"\r\nFIRST ZONE CHOICE WALL CLOCK STOP TIME: ");
  HAL_UART_Transmit(&huart6, txd_msg_buffer, strlen((char*)txd_msg_buffer),1000);
  rcv_intpt_flag = 00;
  HAL_UART_Receive_IT(&huart6, &byte, 2);
  while(rcv_intpt_flag == (00)) {}
  end_time[1] = (byte[0] - '0') * 10 + (byte[1] - '0');

  sprintf((char*)txd_msg_buffer,"\r\nSECOND ZONE CHOICE WALL CLOCK START TIME: ");
  HAL_UART_Transmit(&huart6, txd_msg_buffer, strlen((char*)txd_msg_buffer),1000);
  rcv_intpt_flag = 00;
  HAL_UART_Receive_IT(&huart6, &byte, 2);
  while(rcv_intpt_flag == (00)) {}
  start_time[2] = (byte[0] - '0') * 10 + (byte[1] - '0');
  sprintf((char*)txd_msg_buffer,"\r\nSECOND ZONE CHOICE WALL CLOCK STOP TIME: ");
  HAL_UART_Transmit(&huart6, txd_msg_buffer, strlen((char*)txd_msg_buffer),1000);
  rcv_intpt_flag = 00;
  HAL_UART_Receive_IT(&huart6, &byte, 2);
  while(rcv_intpt_flag == (00)) {}
  end_time[2] = (byte[0] - '0') * 10 + (byte[1] - '0');

  sprintf((char*)txd_msg_buffer,"\r\nTHIRD ZONE CHOICE WALL CLOCK START TIME: ");
  HAL_UART_Transmit(&huart6, txd_msg_buffer, strlen((char*)txd_msg_buffer),1000);
  rcv_intpt_flag = 00;
  HAL_UART_Receive_IT(&huart6, &byte, 2);
  while(rcv_intpt_flag == (00)) {}
  start_time[3] = (byte[0] - '0') * 10 + (byte[1] - '0');

  sprintf((char*)txd_msg_buffer,"\r\nTHIRD ZONE CHOICE WALL CLOCK STOP TIME: ");
  HAL_UART_Transmit(&huart6, txd_msg_buffer, strlen((char*)txd_msg_buffer),1000);
  rcv_intpt_flag = 00;
  HAL_UART_Receive_IT(&huart6, &byte, 2);
  while(rcv_intpt_flag == (00)) {}
  end_time[3] = (byte[0] - '0') * 10 + (byte[1] - '0');

  /*
  pipe_connection[0] = 1;
  pipe_connection[1] = 0;
  pipe_connection[2] = 2;
  pipe_connection[3] = 3;
  pipe_pwm_mode[0] = 0;
  pipe_pwm_mode[1] = 0;
  pipe_pwm_mode[2] = 0;
  pipe_pwm_mode[3] = 0;
  start_time[0] = 0;
  start_time[1] = 2;
  start_time[2] = 4;
  start_time[3] = 6;
  end_time[0] = 2;
  end_time[1] = 4;
  end_time[2] = 6;
  end_time[3] = 8;
  current_time = 0;
  */

  sprintf((char*)txd_msg_buffer,"\r\n\nPRESS BLUE BUTTON TO PRECEED TO RUN MODE");
  HAL_UART_Transmit(&huart6, txd_msg_buffer, strlen((char*)txd_msg_buffer),1000);
  while(HAL_GPIO_ReadPin(GPIOC, B1_Pin)){
	  HAL_GPIO_WritePin(GPIOA, LD2_Pin, GPIO_PIN_SET);
	  HAL_Delay(500);
	  HAL_GPIO_WritePin(GPIOA, LD2_Pin, GPIO_PIN_RESET);
	  HAL_Delay(500);
  }

  sprintf((char*)txd_msg_buffer,"\r\n\nRUN MODE");
  HAL_UART_Transmit(&huart6, txd_msg_buffer, strlen((char*)txd_msg_buffer),1000);
  HAL_GPIO_WritePin(GPIOA, LD2_Pin, GPIO_PIN_SET);


  clock_hours = current_time;
  clock_mins = 0;
  clock_secs = 0;
  wall_clock_hr_update_flag = 1;

  int zone = 0;
  int motor_speed = 0;
  int servo_position[4] = {1000, 1500, 2000, 2500};


    while (1)
    {
    	//potentiometer code
    	ADC_Select_CH(9);
    	HAL_ADC_Start(&hadc1);
    	HAL_ADC_PollForConversion(&hadc1, 1000);
    	uint8_t ADC_CH9 = HAL_ADC_GetValue(&hadc1);
    	HAL_ADC_Stop(&hadc1);

    	current_time = clock_hours;

    	hcsr04_Rx_flag = 0;
    	first_edge = 0;
    	time_edge1 = 0;
    	time_edge2 = 0;
    	time_diff = 0;

    	HCSR04_TRIG_PULSE();
    	while(hcsr04_Rx_flag == 0){};
    	time_diff = time_edge2-time_edge1;
    	distance = (float)time_diff/54;
    	filled = 100-((((float)distance-top_distance)/(bottom_distance-top_distance))*100);
    	sprintf((char*)txd_msg_buffer,"\r\n %d and %d", distance, filled);
    	    			HAL_UART_Transmit(&huart6, txd_msg_buffer, strlen((char*)txd_msg_buffer),1000);


    	if (filled>99) {
    		filled = 99;
    	} else if (filled<0) {
    		filled = 0;
    		empty = 1;
    	}
    	DIGITS_Display(filled);

    	//maybe need to wait until sensor shows 99

    		if(current_time >= start_time[zone] && current_time < end_time[zone]){
    			RGBLED_Run(pipe_connection[zone]);
    			SERVO_Run(servo_position[pipe_connection[zone]]);
    		    switch(pipe_pwm_mode[zone])
    		    {
    		    case 0:
    		    	motor_speed = (((float)ADC_CH9/255)*100);
    		    	rpm = generate_random(((float)ADC_CH9/255)*400,((float)ADC_CH9/255)*500);
    		    	break;
    		    case 1:
    		    	motor_speed = 70;
    		    	rpm = generate_random(325,375);
    		    	break;
    		    case 2:
    		    	motor_speed = 85;
    		    	rpm = generate_random(375,425);
    		    	break;
    		    case 3:
    		    	motor_speed = 99;
    		    	rpm = generate_random(425,475);
    		    	break;
    		    }
    		    if(pipe_connection[zone] == 0){
    		        //motor_speed *= -1;
    		    }
    		    MOTOR_Run(motor_speed);
    		} else if(current_time >= end_time[zone]){
    			zone++;
    		}

    	if(wall_clock_hr_update_flag ==1){


    		if(empty == 1 || zone > 3){
    			sprintf((char*)txd_msg_buffer,"\r\nRESERVOIR EMPTY");
    			HAL_UART_Transmit(&huart6, txd_msg_buffer, strlen((char*)txd_msg_buffer),1000);
    			MOTOR_Run(0);
    			TIM3->CCR1 = 0;
    			TIM3->CCR3 = 0;
    			HAL_GPIO_WritePin(GPIOA, LD2_Pin,GPIO_PIN_SET);
    			while(1)
    			{
    				RGBLED_Run(5);
    				HAL_Delay(500);
    				RGBLED_Run(4);
    				HAL_Delay(500);
    			}
    		}



			sprintf((char*)txd_msg_buffer,"\r\nHour: %d | Zone %d | Motor Speed: %d | Motor RPM: %d | Water Reservoir Depth %d |", clock_hours, zone, motor_speed, rpm, filled);
			HAL_UART_Transmit(&huart6, txd_msg_buffer, strlen((char*)txd_msg_buffer),1000);
			wall_clock_hr_update_flag = 0;
    	}
      /*

  	  // Potentiometer with dc motor code
  	  TIM3_DCVAL = ((float)ADC_CH9/255)*60000;
  	  TIM3->CCR1 = (int)TIM3_DCVAL;

  	  sprintf((char*)txd_msg_buffer, "RPM COUNT: %d \r \n", rpm_tick_count);
  	  HAL_UART_Transmit(&huart6,txd_msg_buffer, strlen((char*)txd_msg_buffer), 1000);


	  //dc motor code
	  TIM3->CCR1 = (int)TIM3_DCVAL;
	  rcv_intpt_flag = 00;
	  HAL_UART_Receive_IT(&huart6, &byte, 1);
	  HAL_UART_Transmit(&huart6,txd_msg_buffer, strlen((char*)txd_msg_buffer), 1000);
	  while(rcv_intpt_flag == (00)) {}
	  */
    /* USER CODE END WHILE */

    /* USER CODE BEGIN 3 */
  }
  /* USER CODE END 3 */
}

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
/* USER CODE BEGIN 4 */
void HAL_UART_RxCpltCallback(UART_HandleTypeDef *huart)
{
    if (huart->Instance == USART6)
    {
        /* Transmit one byte with 100 ms timeout. Transmit the character that was received into the variable called "byte" */
        HAL_UART_Transmit(&huart6, &byte, 1, 100);
        rcv_intpt_flag = 1;
    }
}

void HAL_TIM_IC_CaptureCallback(TIM_HandleTypeDef *htim)
{
if (htim->Instance == TIM4)
    {
        if (htim->Channel == 1) // if the interrupt source is channel 1
        {
            if (first_edge == 0) // if the first value is not captured
            {
                time_edge1 = HAL_TIM_ReadCapturedValue(htim, TIM_CHANNEL_1); // read the first value
                first_edge = 1; // set the first captured as true
            }
   else // if the first is already captured
            {
                time_edge2 = HAL_TIM_ReadCapturedValue(htim, TIM_CHANNEL_1); // read second value
                __HAL_TIM_SET_COUNTER(htim, 0); // reset the counter
                hcsr04_Rx_flag = 1; // set the interrupt flag for result done
            }
        }
    }
}
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

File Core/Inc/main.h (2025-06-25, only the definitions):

#define B1_Pin GPIO_PIN_13
#define B1_GPIO_Port GPIOC
#define B1_EXTI_IRQn EXTI15_10_IRQn
#define DIGIT_A3_Pin GPIO_PIN_0
#define DIGIT_A3_GPIO_Port GPIOC
#define DIGIT_A2_Pin GPIO_PIN_1
#define DIGIT_A2_GPIO_Port GPIOC
#define DIGIT_A1_Pin GPIO_PIN_2
#define DIGIT_A1_GPIO_Port GPIOC
#define DIGIT_A0_Pin GPIO_PIN_3
#define DIGIT_A0_GPIO_Port GPIOC
#define DIGIT_B3_Pin GPIO_PIN_0
#define DIGIT_B3_GPIO_Port GPIOA
#define DIGIT_B2_Pin GPIO_PIN_1
#define DIGIT_B2_GPIO_Port GPIOA
#define USART_TX_Pin GPIO_PIN_2
#define USART_TX_GPIO_Port GPIOA
#define USART_RX_Pin GPIO_PIN_3
#define USART_RX_GPIO_Port GPIOA
#define DIGIT_B0_Pin GPIO_PIN_4
#define DIGIT_B0_GPIO_Port GPIOA
#define LD2_Pin GPIO_PIN_5
#define LD2_GPIO_Port GPIOA
#define DIGIT_B1_Pin GPIO_PIN_0
#define DIGIT_B1_GPIO_Port GPIOB
#define RPM_Tick_Pin GPIO_PIN_2
#define RPM_Tick_GPIO_Port GPIOB
#define RPM_Tick_EXTI_IRQn EXTI2_IRQn
#define BLU_Pin GPIO_PIN_10
#define BLU_GPIO_Port GPIOB
#define HCSR04_TRIG_Pin GPIO_PIN_12
#define HCSR04_TRIG_GPIO_Port GPIOB
#define TMS_Pin GPIO_PIN_13
#define TMS_GPIO_Port GPIOA
#define TCK_Pin GPIO_PIN_14
#define TCK_GPIO_Port GPIOA
#define SWO_Pin GPIO_PIN_3
#define SWO_GPIO_Port GPIOB
#define GRN_Pin GPIO_PIN_4
#define GRN_GPIO_Port GPIOB
#define RED_Pin GPIO_PIN_5
#define RED_GPIO_Port GPIOB

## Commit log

2025-06-25 Initial commit for Drivers
2025-06-25 Initial commit for Reservoir System
    [Pick_and_Place.csv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]

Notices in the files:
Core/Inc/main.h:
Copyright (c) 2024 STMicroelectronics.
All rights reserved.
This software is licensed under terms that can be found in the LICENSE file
